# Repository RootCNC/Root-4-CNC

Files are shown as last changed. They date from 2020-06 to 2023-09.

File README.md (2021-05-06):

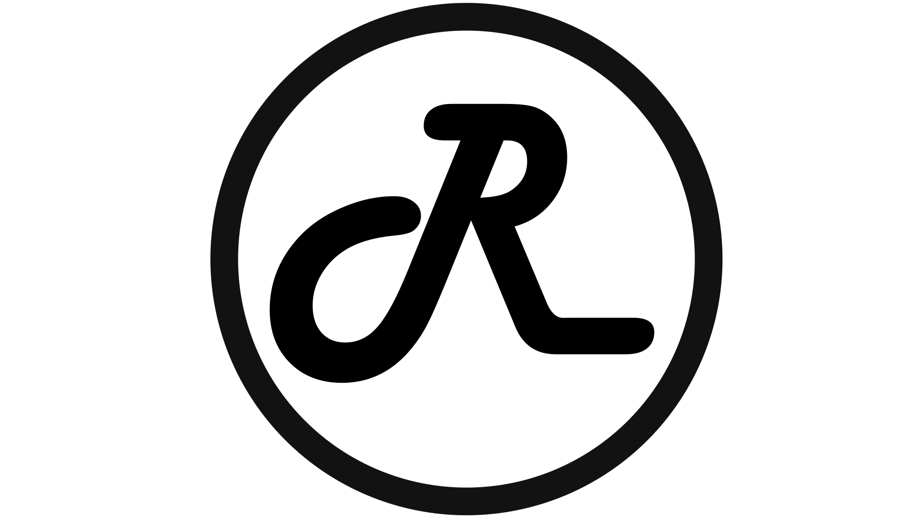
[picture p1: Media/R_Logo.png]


# Root 4 CNC Large Scale 3D Printed CNC Machine
Root 4 is the successor to Root 3 CNC that was my main CNC for a number of years. In fact, there is nothing wrong with my Root 3 CNC (originally named Root 2.1) and it did all my CNC jobs!

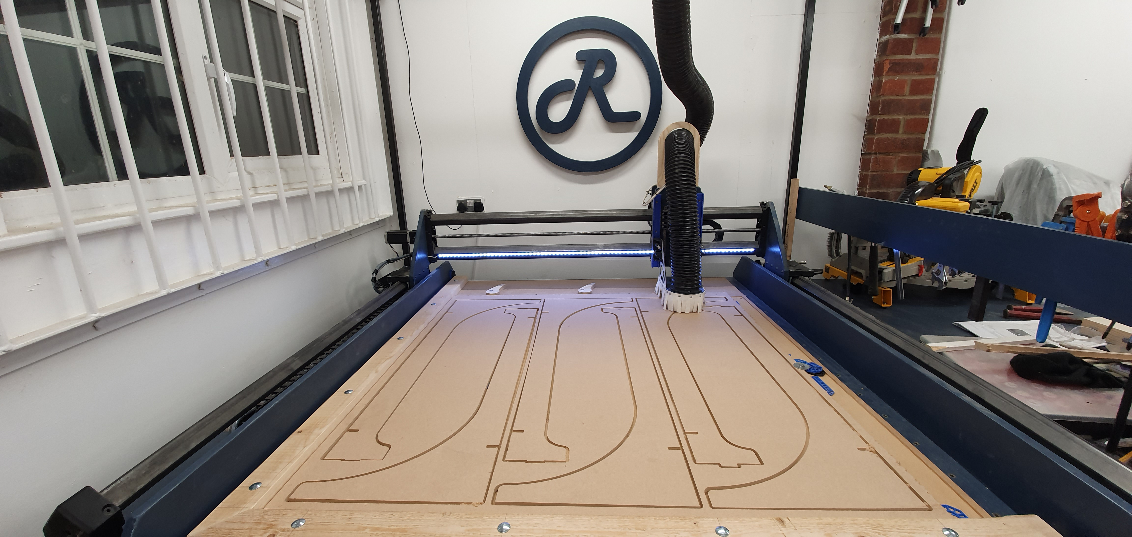
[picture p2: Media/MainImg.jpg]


Root 4 was designed to accommodate larger size 3D printed CNC machine and seeing we’re due to get married soon (Pending lockdown restrictions) – I thought it best to build a bigger one for all the custom wedding ideas we’ve got.

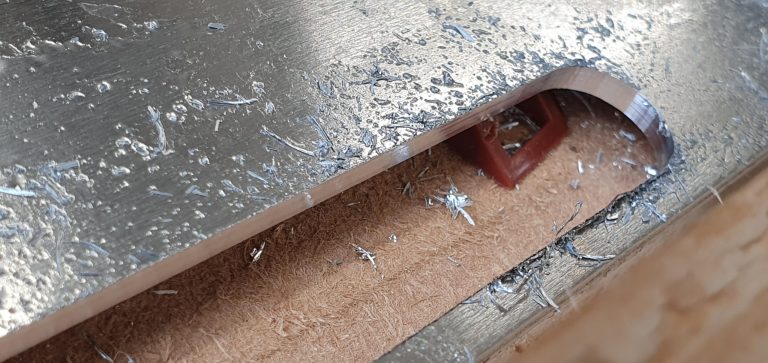
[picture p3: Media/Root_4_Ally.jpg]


The Root 4 follows the core design methodology of simple, cheap, scalable and use common parts for it design. It has also taken inspiration from fellow Root CNC community members who have built their own large-scale 3D printed CNC machines. I do enjoy seeing what you do with these machines, so please consider dropping me an email or post a photo of your build and what you make with this machine.

 ## Key Changes
 A comparison of all the machine can be found on the home page [(LINK)](https://rootcnc.com/)
 1.  Uses 40x40mm Box section
2.  Natively supports balls screws
3.  Has an auto square functionality.
4.  Independent dust shoe.
5.  Stiffer design
6.  Larger working area.

Most of the parts have been tweak from the original Root 3 build but it all can be printed on a standard 200x200mm 3D printer.
## BOM (Bill of Materials)
Bill of Materials can be found [HERE](https://rootcnc.com/root-4-bill-of-materials/)

## Working Area

    What is the working area of the Root 4 CNC Machine?

    What length of 40x40mm Box section do I required?

Please see this file: [Here](https://github.com/RootCNC/Root-4-CNC/blob/master/Working%20Area.xlsx)

For a comparison of **SFU1605 Ball screw length** VS **Box Section Length** VS **working area** (taking into account side panel thickness).

For my build I used 1500mm long ballscrew for both X and Y Axis with a total working area of **1204mm by 1190mm** (XY) with a Z travel of 158mm as standard. (Z-Axis is **not** user configurable)

## Videos
Youtube Videos can be found  [Here](https://www.youtube.com/sailorpete12)

Time Lapse Voice over video series  [Here](https://www.youtube.com/playlist?list=PL5hghy18PulVQLauypyohv9KJJGx_RQMZ)
### Assembly Videos
(http://www.youtube.com/watch?v=JoyMASlxskQ "")
### Detailed Videos
(http://www.youtube.com/watch?v=6tHN1ftT5lI "")
## In action!
(http://www.youtube.com/watch?v=OX2FyZha2Zk "")
(http://www.youtube.com/watch?v=DdyRnfVLRq8 "")
(http://www.youtube.com/watch?v=58G44EHEyc4 "")

## License

This project is licensed under the Creative Commons 4.0 license with 
Attribution-NonCommerial-ShareAlike see `LICENSE.txt` for details

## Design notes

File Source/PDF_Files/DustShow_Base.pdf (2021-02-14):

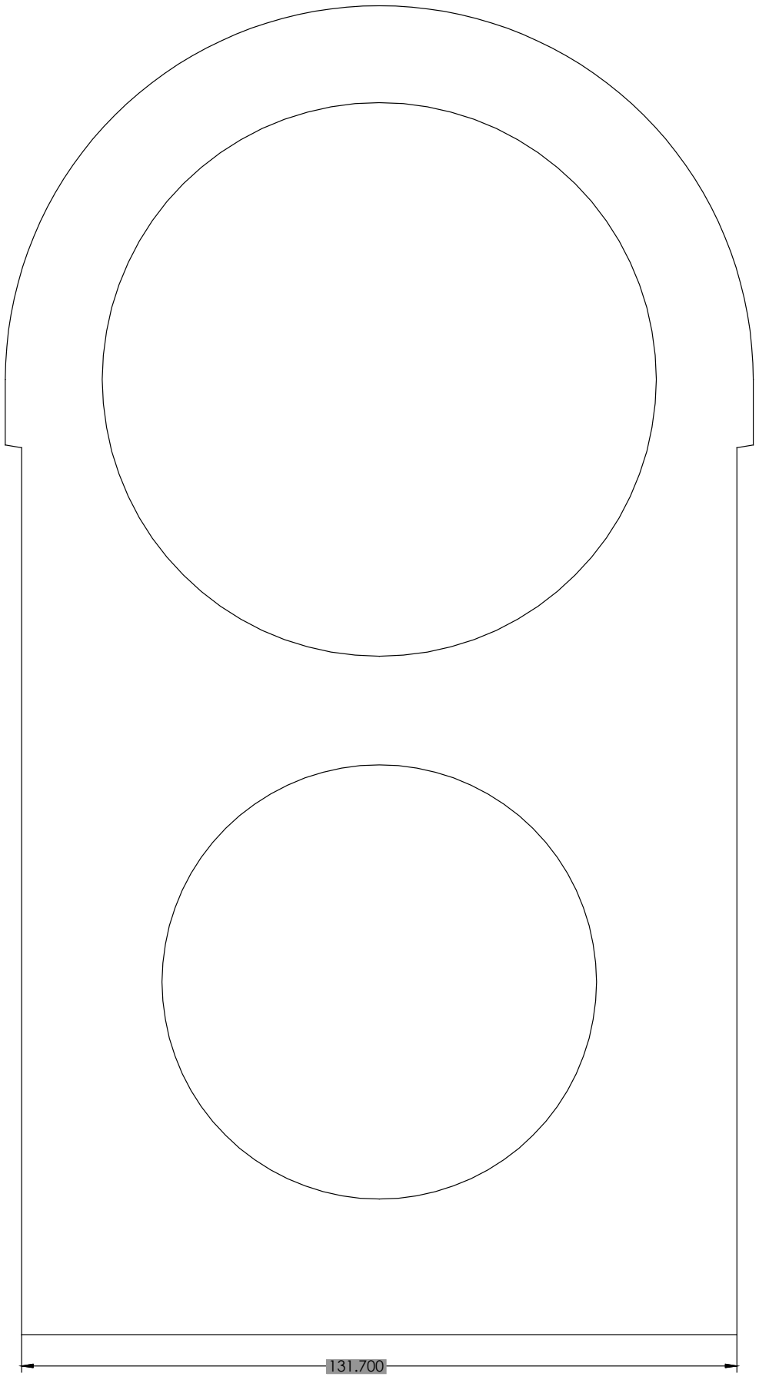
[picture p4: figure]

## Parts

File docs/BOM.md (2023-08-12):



# 3D Printed Parts required

| 3D Printed Parts | Required | QTY |
|---|---|---|
| DustShoe_100mmHose | NO | 1 |
| DustShoe_RailClamp_Left | NO | 1 |
| DustShoe_RailClamp_Right | NO | 1 |
| DustShoe_T_SlotTrack | NO | 2 |
| Spindle_Mount_65mm | YES | 1 |
| X_Axis_DragChainBrace | YES | 1 |
| X_Axis_DragChainBrace (Mirrored) | YES | 1 |
| X_Axis_DragChainMountXCarriage | YES | 1 |
| X_Axis_Mount_FF | YES | 1 |
| X_Axis_Mount_FK | YES | 1 |
| X_Axis_NEMA23_50mmSpacerFK12 | YES | 1 |
| XY_Carriage | YES | 8/4* |
| XY_Carriage_Coach | YES | 4* |
| XY_Axis_BallScrewMount | YES | 3 |
| XY_Axis_BallScrewMount+0.25 | YES | 3** |
| Y_Axis_DragChainCarriageMount | YES | 1*** |
| Y_Axis_Mount_FF12 | YES | 2 |
| Y_Axis_Mount_FK12 | YES | 2 |
| Y_Axis_NEMA23_50mmMotorSpacer | YES | 2 |
| Z_Axis_MotorMount | YES | 1 |

(\*) When Coach bolts are used

(\*\*) Only required if the standard is too loose

(\*\*\*) Can be mirrored for the Drag chain to be mounted on the other side

# Panels
| Item | QTY | Link|
|---|---|-----|
|DustShoe_Side| 2|Root CNC Store|
|DustShoe_Base|1|Root CNC Store|
|Side_Panel_Left_FK|1|[Root CNC Store](https://rootcnc.com/product/root-4-side-panel/)|
|Side_Panel_Right_FF|1|[Root CNC Store](https://rootcnc.com/product/root-4-side-panel/)|
|Z_Axis_WoodPanel_Front|1|Root CNC Store|
|Z_Axis_WoodPanel_Rear|1|Root CNC Store|

# Electronics/ Electro Mechanical
| Item | Required | QTY | Link|
|---|---|---|-----|
| 4 Axis CNC Router Kit 3.0 Nm 425o/in Nema 23 | Yes | 1 | [LINK](https://www.omc-stepperonline.com/4-axis-cnc-router-kit-3-0-nm-425oz-in-nema-23-stepper-motor-driver-power-supply-4-dm542y-23he45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)
|1.5KW Spindle with VFD|Yes|1|[LINK_1](https://s.click.aliexpress.com/e/_dX0JKm3) [LINK_2](https://s.click.aliexpress.com/e/_dT4xs63) [LINK_3](https://s.click.aliexpress.com/e/_dSjt6gr) [LINK_4](https://s.click.aliexpress.com/e/_dSUhh43)
|Micro Switch SPDT micro switch V4 KW11i|Yes|6|[LINK UK](https://amzn.to/31Kf1wC) [LINK](https://s.click.aliexpress.com/e/_ATnQCz)| 
|12V or 24V PSU (For Controller power + any lights) |Yes|1|[12V_LINK_UK](https://amzn.to/2HxYvIS) [12V_lINK](https://s.click.aliexpress.com/e/_AACYyd)| 
|Electrical Cabinet (size greater than 400x400x200mm) |No|1|| 
|Aviation plug (GX12) |No|x|[LINK_UK](https://amzn.to/31LBPfl)[LINK](https://s.click.aliexpress.com/e/_AtqbWz)|

# Motion
| Item | Required | QTY | Link|
|---|---|---|-----|
|608 Bearings | Yes | 38 |[LINK_UK](https://amzn.to/3dWB9c6) [LINK](https://s.click.aliexpress.com/e/_ATuujF)|
|SFU1605 L300 (Z-Axis) | Yes | 1 |[LINK_UK](https://amzn.to/3osWWNp) [LINK](https://s.click.aliexpress.com/e/_AOHs9J)|
|SFU1605 L### (X-Axis) | Yes | 1 |[LINK_UK](https://amzn.to/35AbBOe) [LINK](https://s.click.aliexpress.com/e/_9zA1ff)|
|SFU1605 L### (Y-Axis) | Yes | 2 |[LINK_UK](https://amzn.to/35AbBOe) [LINK](https://s.click.aliexpress.com/e/_9zA1ff)|
|FK12 Bearing | Yes | 3 |[LINK_UK](https://amzn.to/35zBhKN) [LINK](https://s.click.aliexpress.com/e/_9v05o1)|
|FF12 Bearing | Yes | 3 |[LINK_UK](https://amzn.to/35zBhKN) [LINK](https://s.click.aliexpress.com/e/_9v05o1)|
|BK12 | Yes | 1 |[LINK](https://s.click.aliexpress.com/e/_9v05o1)|
|BF12 | Yes | 1 |[LINK](https://s.click.aliexpress.com/e/_9v05o1)|
|MGN12 250mm + (MGN12C x2) | Yes | 2 |[LINK](https://s.click.aliexpress.com/e/_ALbQTF)|
|R38 18mm x 37mm Black Drag Chain 1M | Yes | CNC Size dependant |[LINK_UK](https://amzn.to/37J6PAH)  [LINK](https://s.click.aliexpress.com/e/_9hJS33)|
|T-track [300mm, Blue] | Yes | 2 |[LINK_UK](https://amzn.to/3mkDBvK) [LINK](https://s.click.aliexpress.com/e/_9x8Pnf)|
|CNC shaft couplers Spider Jaw (10mm to 10mm)| Yes | 3 |[LINK_UK](https://amzn.to/3jxH1tx) [LINK](https://s.click.aliexpress.com/e/_AP8YPT)|
|HTD 3M Round Tooth Timing Belt Pulley 10MM Bore 36T| Yes | 1 |[LINK](https://s.click.aliexpress.com/e/_9hO2OZ)|
|HTD 3M Round Tooth Timing Belt Pulley 10MM Bore 36T*| Yes | 1 |[LINK](https://s.click.aliexpress.com/e/_9hO2OZ) |
|HTD 3M Round Tooth Timing Belt 9mm Wide 474-3m-09| Yes | 1 |[LINK_UK](https://amzn.to/2Tu7xcu) [LINK](https://s.click.aliexpress.com/e/_9HpJZj)

(\*) Dependant on stepper motor selection - This configuration will work for the above stepper motor from OMC Stepper Motor Online
# Hardware
Below is guide on the QTY required/ the pack sizes I brought to assemble the Root 4 CNC
| Item | Required | QTY | Link|
|---|---|---|-----|
|40mm box section (50mm shorter than X lead screw) *|Yes|2||
|40mm box section (70mm shorter than Y lead screw ONLY WITH 18MM SIDE PANELS!) *|Yes|2||
|M3 Insert Nut (Z-Axis Linear Guilds) | Yes | 20  | | 
|M3 X 14MM Allen Hex Head A4 (Z-Axis Carriage to linear guilds) | Yes | 16  | | 
|M3 X 16MM Allen Hex Head A4 (Z-Axis linear Guilds) | Yes | 20  | | 
|M4 Knurled Thumb Nut (Used for Independent height dust shoe) | No | 4  | | 
|M4 Nut | Yes | 100  | | 
|M4 Penny Washer | Yes | 100  | | 
|M4 X 10mm Socket Cap Head  | Yes | 100  | | 
|M4 X 20mm Socket Cap Head  | Yes | 100  | | 
|M4 X 25mm Socket Cap Head  | Yes | 100  | | 
|M4 X 30mm Socket Cap Head  | Yes | 100  | | 
|M4 X 40MM COUNTERSUNK | Yes | 100  | | 
|M4 X 40mm Socket Cap Head  | Yes | 100  | | 
|M5 Knurled Thumb Nut (Used for Independent height dust shoe) | No | 2  | | 
|M5 Nuts  | Yes | 100  | | 
|M5 Washer | Yes | 100  | | 
|M5 x 16mm Socket Cap Head (To secure the Ball screw to Ball screw block, Z-Carriage) | Yes | 28  | | 
|M5 x 20mm Socket Cap Head | Yes | 50  | | 
|M5 x 55mm Socket Cap Head | Yes | 8 | |
|M5 x 75mm (Used for independent height dust shoe) | Yes | 4  | | 
|M5 X 90MM A2 STAINLESS STEEL CAP HEX HEAD | Yes | 20  | | 
|M6 Bed Insert nut | No | 200  | | 
|M6 Insert Nut (10MM Long Furniture Insert) | Yes | 6  | | 
|M6 x 10 mm Socket Cap Head | Yes | 20  | | 
|M6 x 40mm Socket Cap Head (Z-Axis Ball screw bearing block) | Yes | 6  | | 
|M8 loc nut | Yes | 100  | | 
|M8 Nut | Yes | 200  | | 
|M8 Washer | Yes | 200  | | 
|M8 x 100mm (Coach or STD) Bolt | Yes | 16  | | 
|M8 X 25MM  | Yes | 38  | | 

(\*) Please see this file [Here](https://github.com/RootCNC/Root-4-CNC/blob/master/Working%20Area.xlsx). For a comparison of **SFU1605 Ball screw length** VS **Box Section Length** VS **working area** (taking into account side panel thickness).

# MISC Items
| Item | Required | QTY | Link|
|---|---|---|-----|
|Mist Coolant Lubrication Spray System Unit (Used for Airline to Spindle - Aluminium machining)| No |1 | |
|Pneumatic Air Solenoid Valve 2Way (Used for Airline to Spindle - Aluminium machining)| No |1 | |
|T-track [300mm, Blue]| No |2 | |
|Yellow Semi Rigid Nylon Tubing (Used for Airline to Spindle - Aluminium machining)| No |1 | |
|Male Swivel Elbow Pneumatic Push-In Fitting Connector for Air. Size 8mm x 1/4"| No |x | |

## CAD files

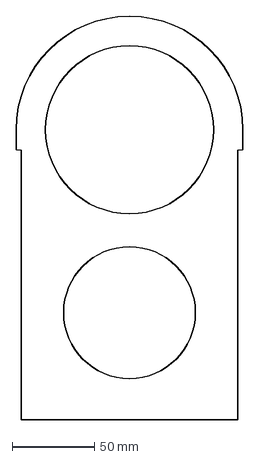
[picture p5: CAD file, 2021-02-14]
Source/DXF_Files/DustShoe_Base.DXF
137.7 x 244.9 mm

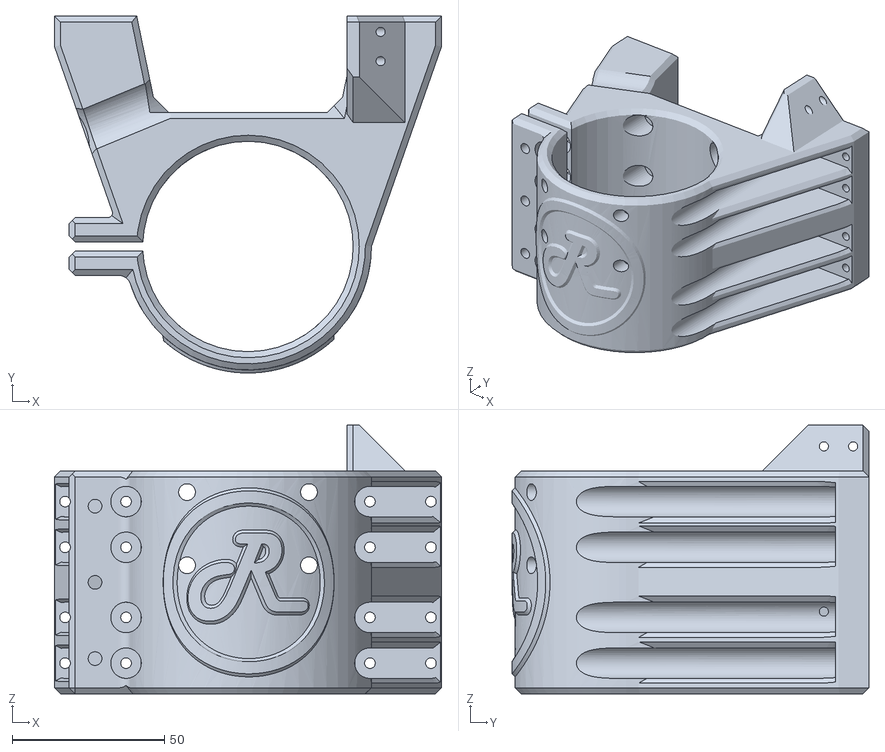
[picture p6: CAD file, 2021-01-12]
Source/STL_Files/Spindle_Mount_69mm.STL
127.0 x 117.1 x 88.2

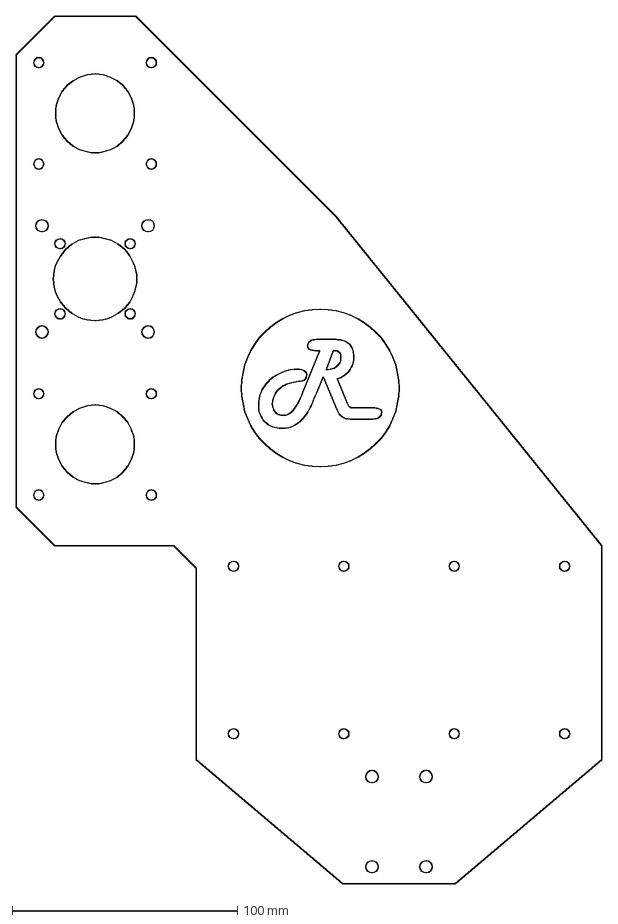
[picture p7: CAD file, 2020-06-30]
Source/DXF_Files/Side_Panel_Left_FK.DXF
260.0 x 385.0 mm

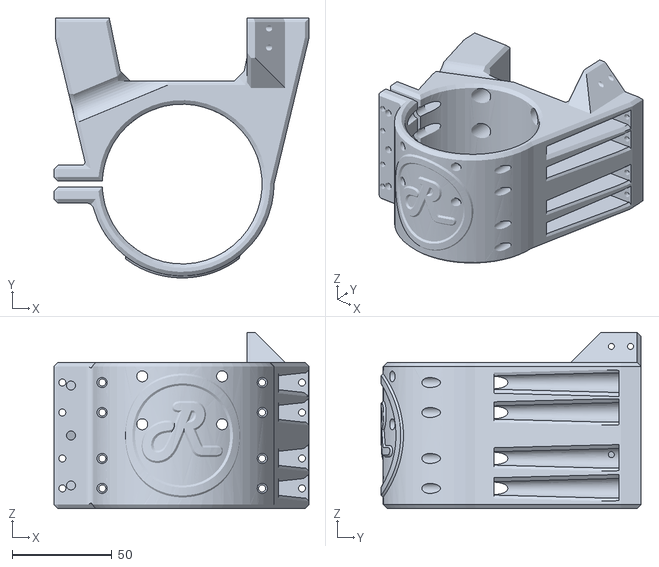
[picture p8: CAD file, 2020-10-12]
Source/STL_Files/Spindle_Mount_80mm.STL
127.7 x 130.1 x 88.2

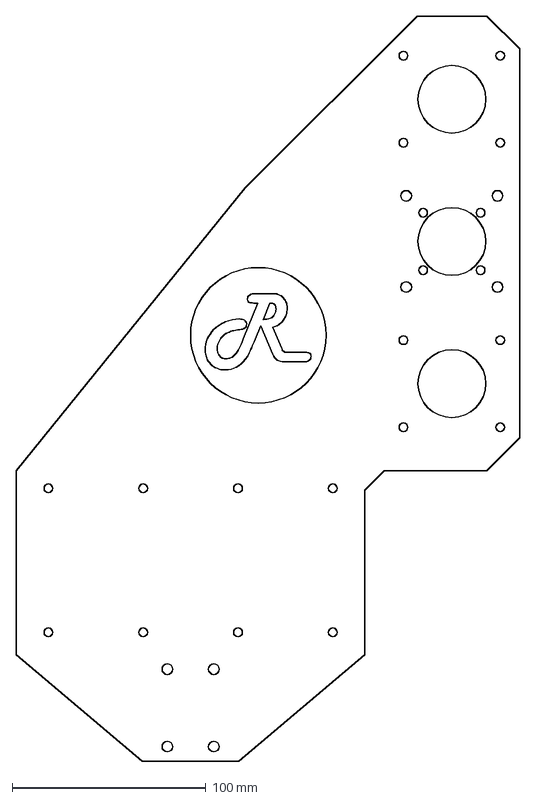
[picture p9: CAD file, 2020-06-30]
Source/DXF_Files/Side_Panel_Right_FF.DXF
260.0 x 385.0 mm

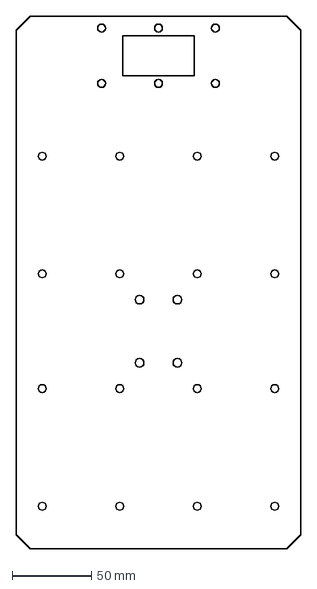
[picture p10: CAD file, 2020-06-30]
Source/DXF_Files/Z_Axis_WoodPanel_Rear.DXF
180.0 x 337.0 mm

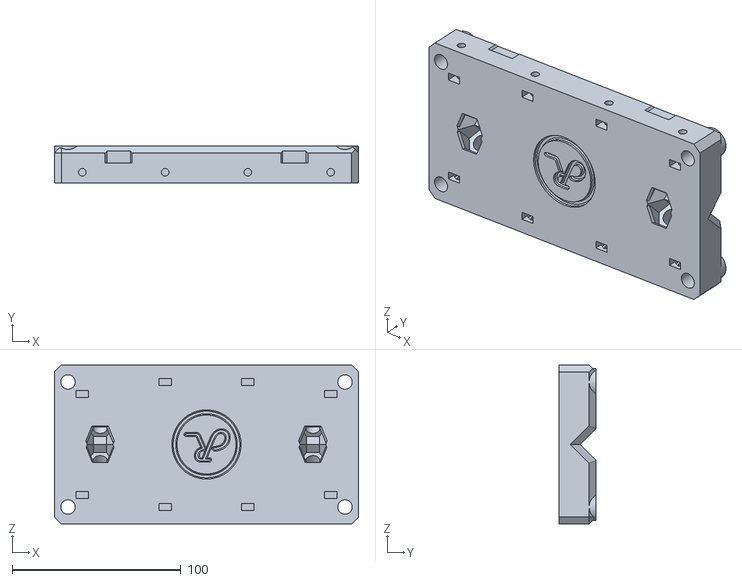
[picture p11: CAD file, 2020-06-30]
Source/STL_Files/XY_Carriage.STL
180.0 x 22.2 x 94.0

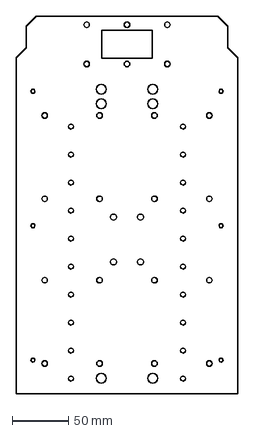
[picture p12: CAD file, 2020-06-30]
Source/DXF_Files/Z_Axis_WoodPanel_Front.DXF
198.0 x 337.0 mm

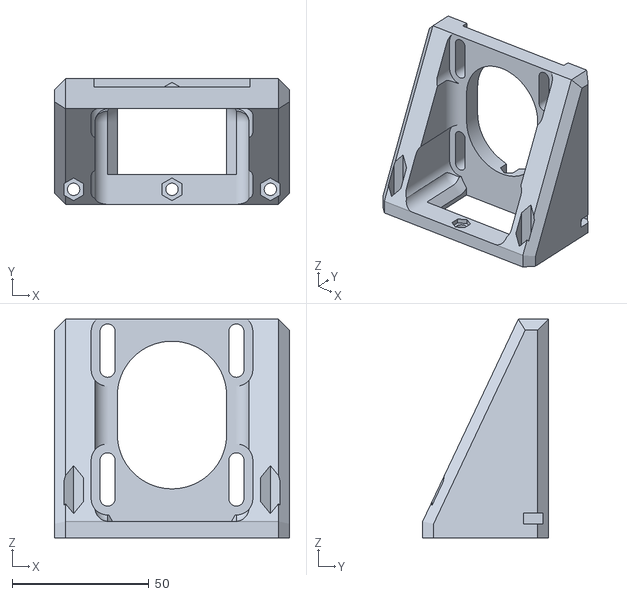
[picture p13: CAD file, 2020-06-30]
Source/STL_Files/Z_Axis_MotorMount.STL
86.0 x 46.0 x 80.0

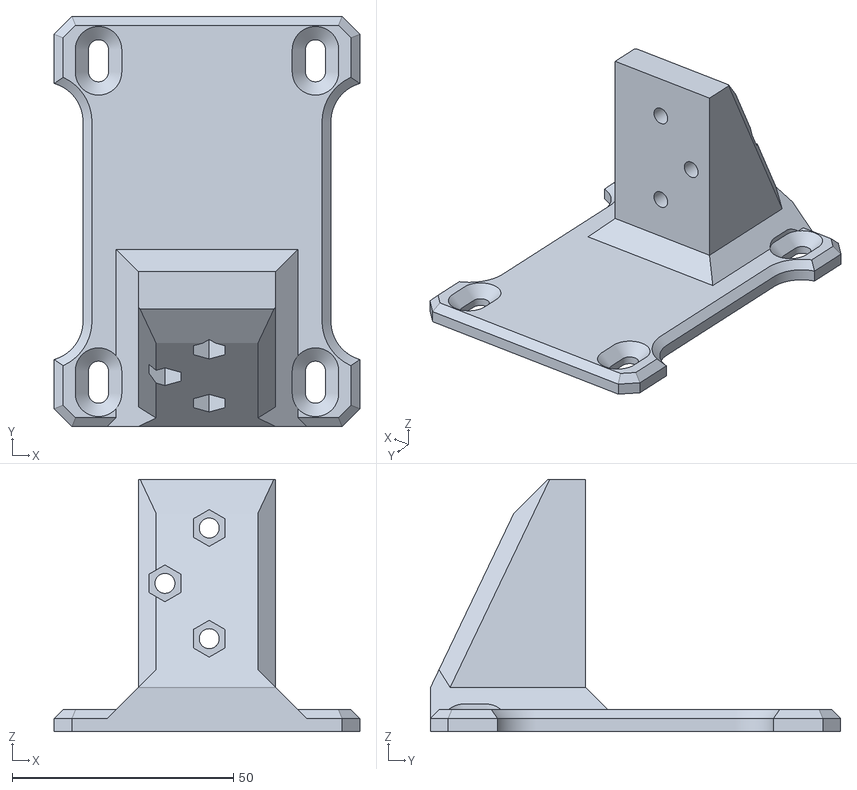
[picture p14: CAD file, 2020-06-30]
Source/STL_Files/X_Axis_DragChainMountXCarriage.STL
69.0 x 92.6 x 57.0

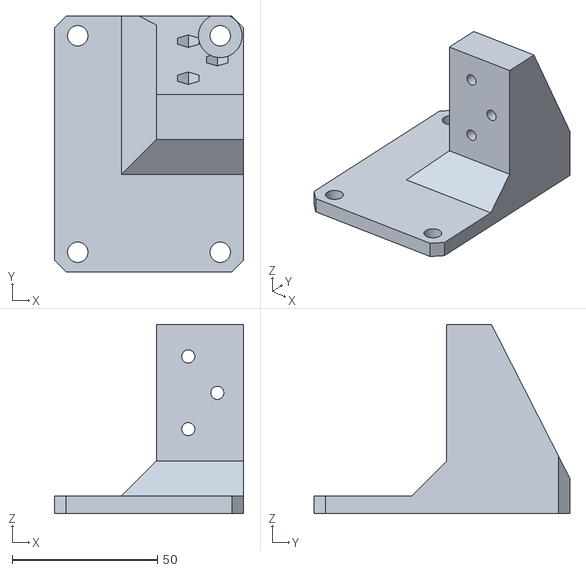
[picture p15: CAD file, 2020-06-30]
Source/STL_Files/Y_Axis_DragChainCarriageMount.STL
65.0 x 88.0 x 65.0

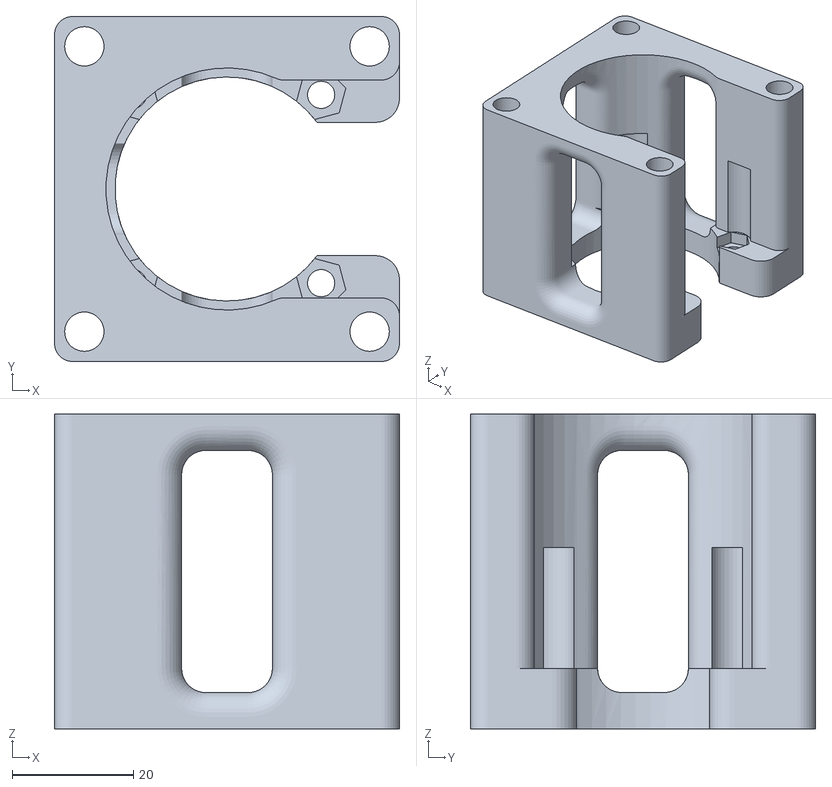
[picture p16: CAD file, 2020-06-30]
Source/STL_Files/X_Axis_NEMA23_50mmSpacerFK12.STL
57.0 x 57.0 x 52.0

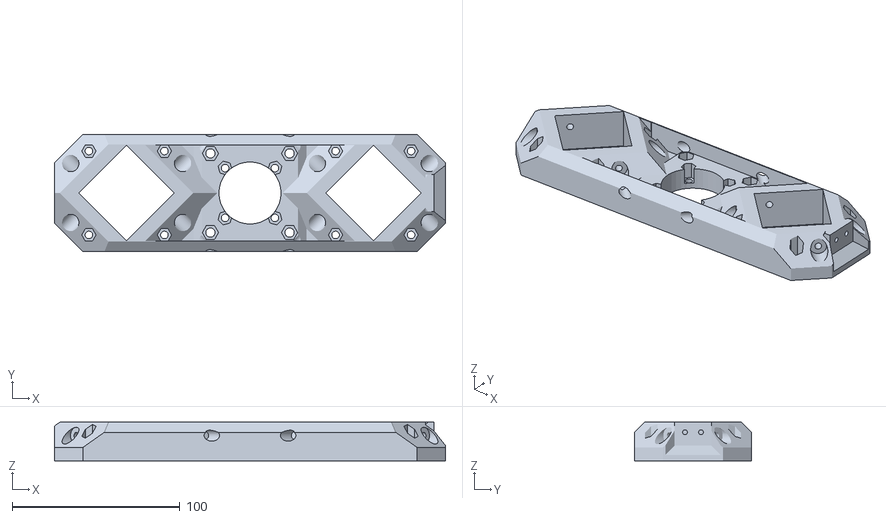
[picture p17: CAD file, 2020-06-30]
Source/STL_Files/X_Axis_Mount_FF.STL
233.0 x 70.0 x 23.0

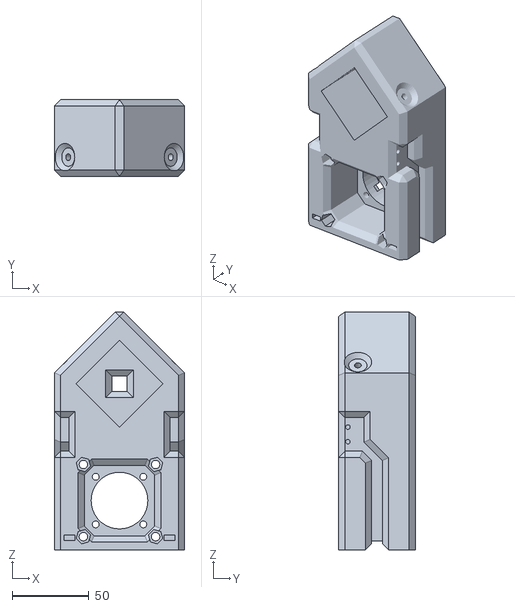
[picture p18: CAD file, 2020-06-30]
Source/STL_Files/Y_Axis_Mount_FF12.STL
85.0 x 50.0 x 155.4

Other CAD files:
Source/STL_Files/DustShoe_T_SlotTrack.STL
Source/STL_Files/Y_Axis_NEMA23_50mmMotorSpacer.STL
Source/STL_Files/X_Axis_Mount_FK.STL
Source/STL_Files/X_Axis_DragChainBrace.STL
Source/DXF_Files/DustShoe_Side.DXF
Source/STL_Files/DustShoe_Side.STL
Source/STL_Files/XY_Axis_BallScrewMount+0.25.STL
Source/STL_Files/XY_Axis_BallScrewMount.STL
Source/STL_Files/XY_Carriage_Coach.STL
Source/STL_Files/Y_Axis_Mount_FK12.STL

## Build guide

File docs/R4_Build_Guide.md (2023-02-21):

---
title: Root 4 Assembly Guide
description: Root 4 Assembly Guide 
published: true
date: 2022-06-28T21:37:30.411Z
tags: root 4, r4, guide
editor: markdown
dateCreated: 2022-05-24T19:30:47.756Z
---

# Root 4 CNC Build Guide

## Before you get building/printing

## Key info
1.  Build area and machine size is all dependent on the size of ball screws and box section. Please see this file: [Here](https://github.com/RootCNC/Root-4-CNC/blob/master/Working%20Area.xlsx)
2.  North American builders should see the gotchas below
3.  Ballpark price is dependent on your build size and upgrade/quality-of-life choices you make, but expect somewhere in the realm of £900-1200 GBP, $1200-1500 USD, $1500-2000 AUD

## Gotchas before starting
1. Make sure you have access to metric box section in your country before you start printing parts.
2. If you need Imperial, then there is a [branch of files for 1.5 inch box section to print instead](https://github.com/RootCNC/Root-4-CNC/tree/38mm-Dev/Source/STL_Files/38.1x38.1mm%20Box%20Section%20%281.5x1.5%20inch%29)

## Printing parts

### Printing considerations
1. If you have access to a 0.6mm nozzle, this will significantly decrease the time needed to print, while also strengthening the parts due to the line widths. **Worth buying one just for this project alone.**
2. Similarly, larger layer heights afforded by the 0.6mm nozzle will give you more strength and speed up the print
3. Rigidity of material matters as much as strength for a number of parts. Consider using a modified PLA blend (commonly known as PLA+, pro PLA etc.) for parts where rigidity is paramount (see table below) and PETG for parts where sheer strength is more important.
4. More walls is better than more infill if you want strong parts
5. Use supports really carefully - some models have quite complex segments for nestling hex nuts, and you don't want to be pulling supports out of those spots. Use support blockers to ensure those channels are kept clear.
6. Tune your printer to give you accurate hole diameters. Check every hole after printing before moving on to print a duplicate part.

### Recommended print settings
1. 2-3 walls/perimeters of 0.6mm width
2. 0.3+ layer heights - this can be achieved with a 0.4mm nozzle, but better with a 0.6mm nozzle. Adaptive layers not recommended.
3. 3-4 bottom/top layers - whether you choose 3 or 4 will depend on whether there are mounting holes pushing against the top/bottom.
4. 30-40% infill. The more a piece is likely to be compressed, the more infill. If approaching 40% infill, consider if you'd be better off adding an additional wall instead.
5. None of these parts need to be pretty, so feel free to print as fast as you can, just ensure that your holes are accurate. Use hole horizontal expansion to your advantage to perfect your hole sizes.

## Planning your build
- Use the [working area file](https://github.com/RootCNC/Root-4-CNC/blob/master/Working%20Area.xlsx) to determine what size ball screws and box section you need to order.
- What do you intend to cut on your CNC? Consider whether a square build is most suitable, or whether a wider X axis with a shallower Y axis will mean your CNC takes up a smaller footprint, but can allow larger stock to be fed through from front to back for the occasional larger project.
- Going wider in the X axis is cheaper than going longer in the Y axis, as you only have a single ball screw on the X axis, but the amount of square box section is the same.
- Do you want the lightness and stiffness of aluminium square hollow section (will tend to cost more) or the beefy weight of steel (tends to be cheaper if not shipped). Steel's density will absorb more vibrations from the machine than aluminium will, and it's weight will go a small way to minimising deflection.

## Building your platform
- Decide what base/platform you're going to build your CNC upon. The Root 4 is different to the previous Root machines in that the machine isn't necessarily designed to be portable and doesn't rest on feet. This means you can really make the most of having a rigid platform.
- Keeping the platform square and flat over the life of the machine is essential. There are a few ways to do this:
  - You can follow the method in the videos of welding a metal frame to mount plywood to. This is the simplest and likely most cost effective method. The metal frame will stop the plywood from warping over time and also give you a frame for mounting controls/enclosure on.
  - If you intend to make a timber frame, then you will be best served building a 'torsion box' table to keep the surface as flat as possible. This can be done with an MDF core and two sheets of plywood - just make sure you have solid corners to be able to countersink mount holes for your Y axis mounts.
- Make sure your platform is deep enough to accommodate your stepper motors on their standoffs without hanging over the back of your CNC.
- Make sure your platform is wide enough to accommodate mounting your cable chain outside the path/width of the Y carriage.
- Do you want to use alcohol/alcohol-based cutting fluid for milling metals? Make sure any finish you put on your wood is not going to break down with alcohol or other solvents.

## High level overview - Order of construction
1. Carriages - build them up according to the video, slide them onto the tubes, ensure they have no play.
2. Mount Y axis ball screw mount and aluminium ball screw nut housing onto the Y axis side panels (not essential to do now, but does make things easier)
3. Mount Y axis side panels onto Y carriages (far easier to do now than trying to get in under already mounted square tubes)
4. Mark out and drill your Y axis mount holes. Screw down the rear mount.
5. Slide your hollow box section into the Y axis mount (ensuring the carriages are already on) and screw in the front Y axis mount
6. Prepare the Z axis front panel with rivnuts and threaded inserts, screw on your linear rails, leave everything else off
7. Mount X axis ball screw mount and aluminium ball screw nut housing onto the rear face of the Z axis front panel
8. Slide X axis mounts onto hollow box section (ensuring the carriages are already on) and lay it down on your table
9. Mount the Z axis front panel onto the X carriages
10. Wind the X axis ball screw nut into the centre of the screw. Position the X axis ball screw in place between the box section, ensuring the ball screw nut is on the correct side to nest inside the aluminium housing, but also ensuring the end machined for the fixed ball screw mount (FF) is on the left. Screw the ball screw nut into the housing
11. Flip the X axis setup over and mount the Z axis rear panel
12. Resting your X axis bottom carriage on a box or something of suitable height for support, screw the X axis mounts in place on your side panels
13. Attach your X axis ball screw mounts
14. TBC

## License

This project is licensed under the Creative Commons 4.0 license with 
Attribution-NonCommerial-ShareAlike see `LICENSE.txt` for details

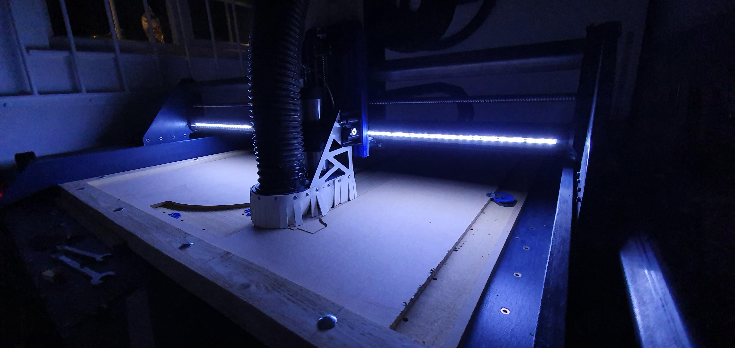
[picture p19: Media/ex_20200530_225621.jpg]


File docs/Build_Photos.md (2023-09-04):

---
title: Root 4 Build Photos
description: Build Photos for the Root 4
published: true
date: 2022-06-28T22:24:57.245Z
tags: root 4, how to print
editor: markdown
dateCreated: 2022-06-28T22:17:17.168Z
---

# Build Photos
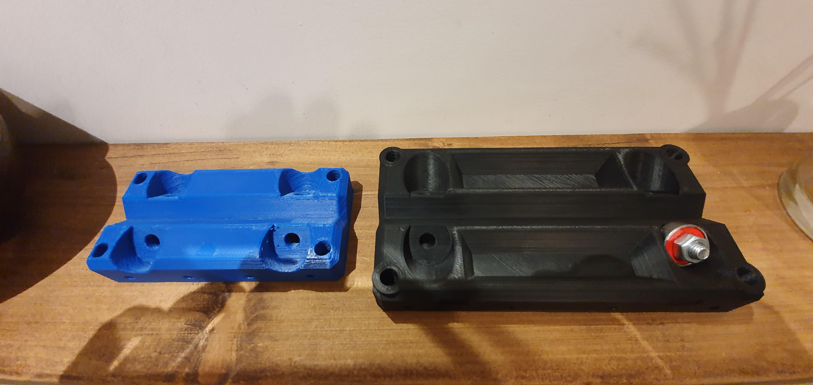
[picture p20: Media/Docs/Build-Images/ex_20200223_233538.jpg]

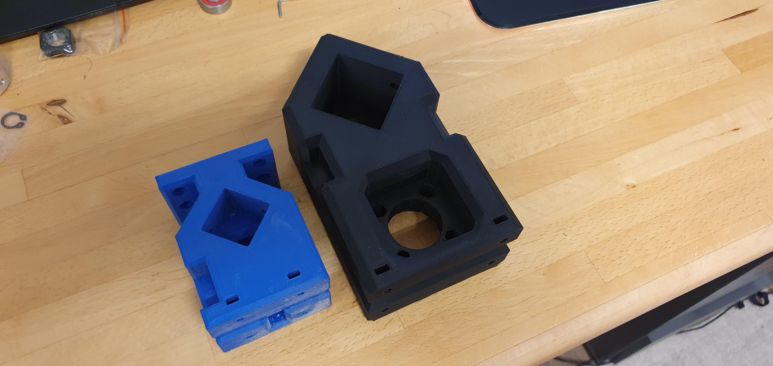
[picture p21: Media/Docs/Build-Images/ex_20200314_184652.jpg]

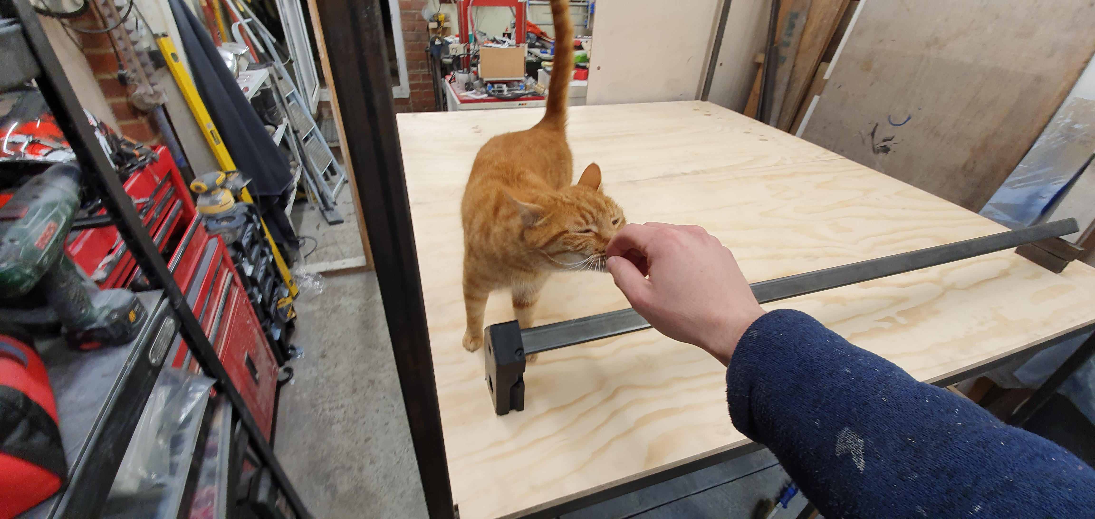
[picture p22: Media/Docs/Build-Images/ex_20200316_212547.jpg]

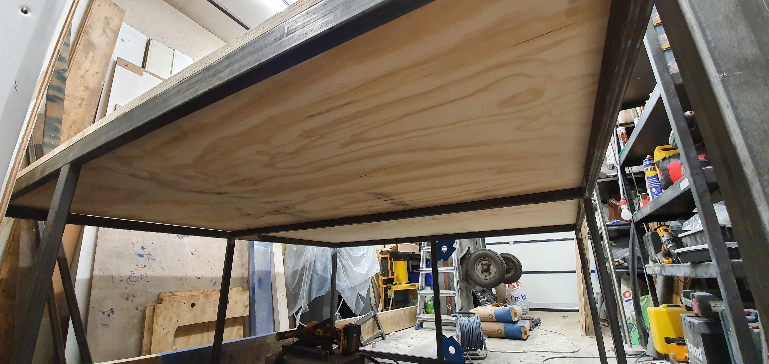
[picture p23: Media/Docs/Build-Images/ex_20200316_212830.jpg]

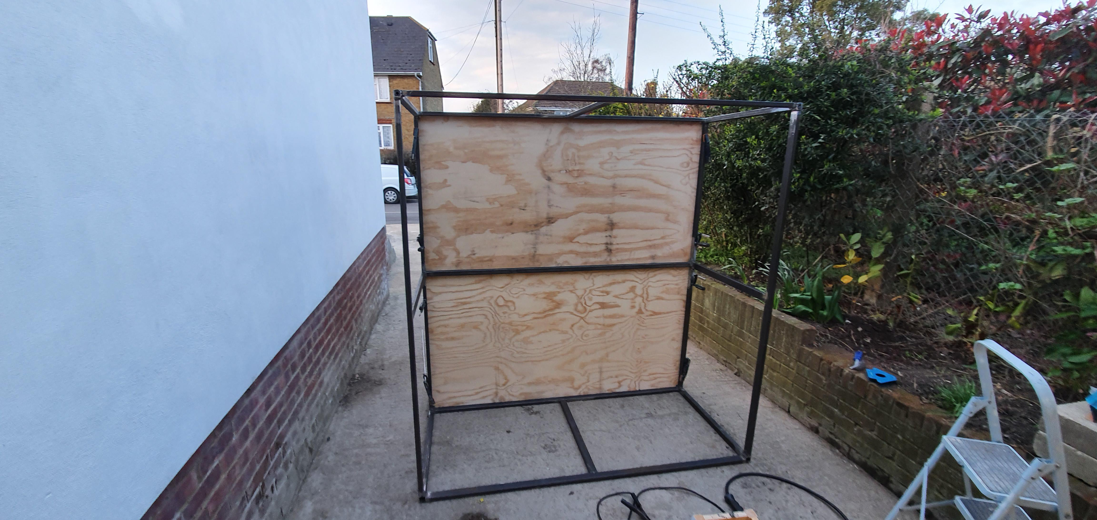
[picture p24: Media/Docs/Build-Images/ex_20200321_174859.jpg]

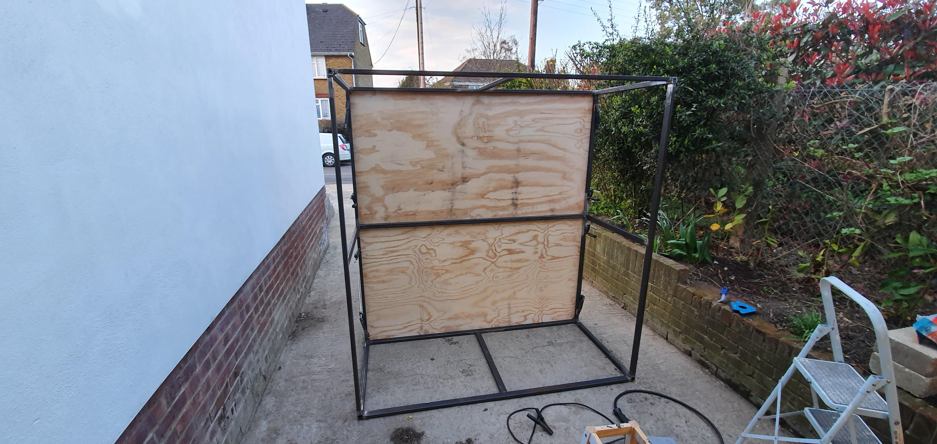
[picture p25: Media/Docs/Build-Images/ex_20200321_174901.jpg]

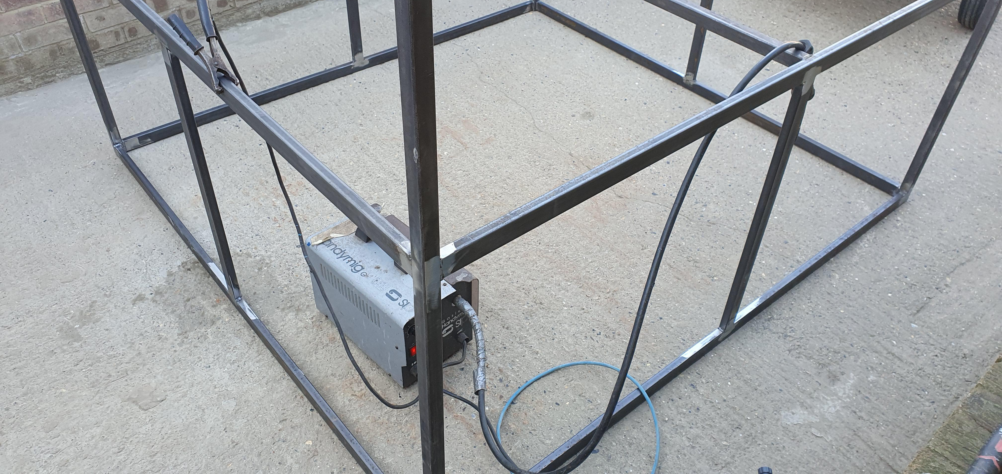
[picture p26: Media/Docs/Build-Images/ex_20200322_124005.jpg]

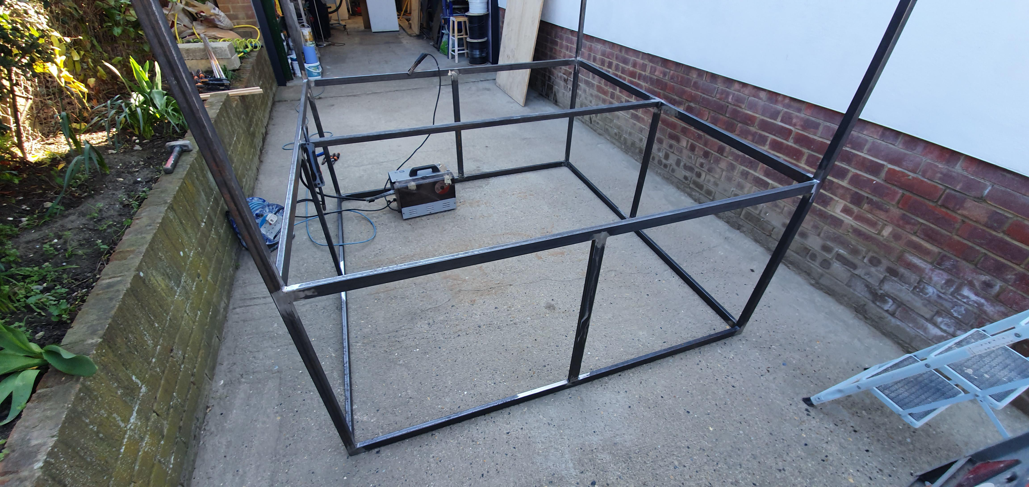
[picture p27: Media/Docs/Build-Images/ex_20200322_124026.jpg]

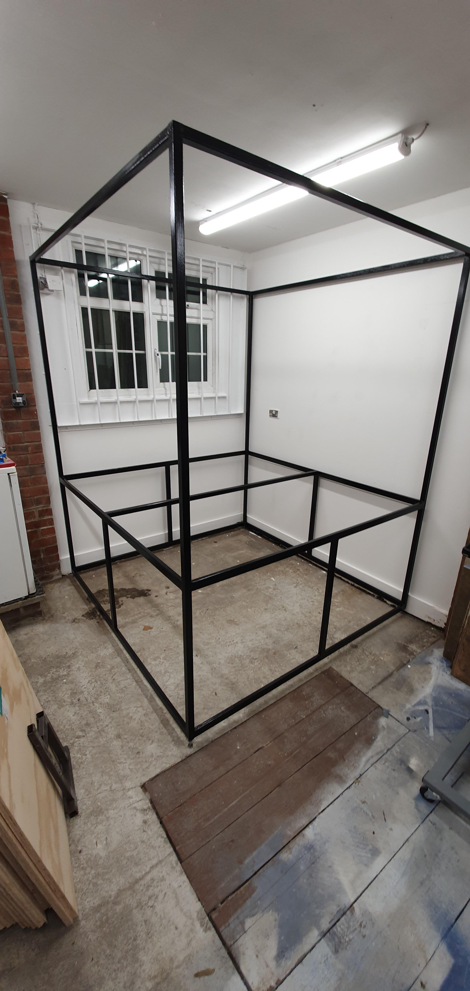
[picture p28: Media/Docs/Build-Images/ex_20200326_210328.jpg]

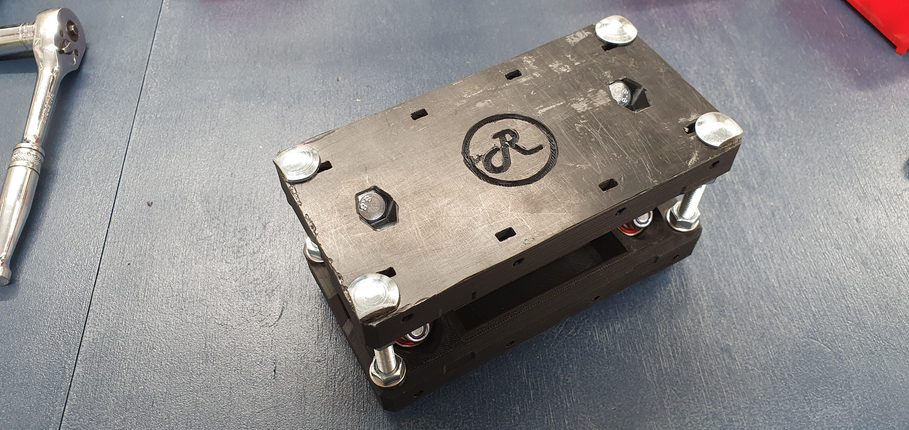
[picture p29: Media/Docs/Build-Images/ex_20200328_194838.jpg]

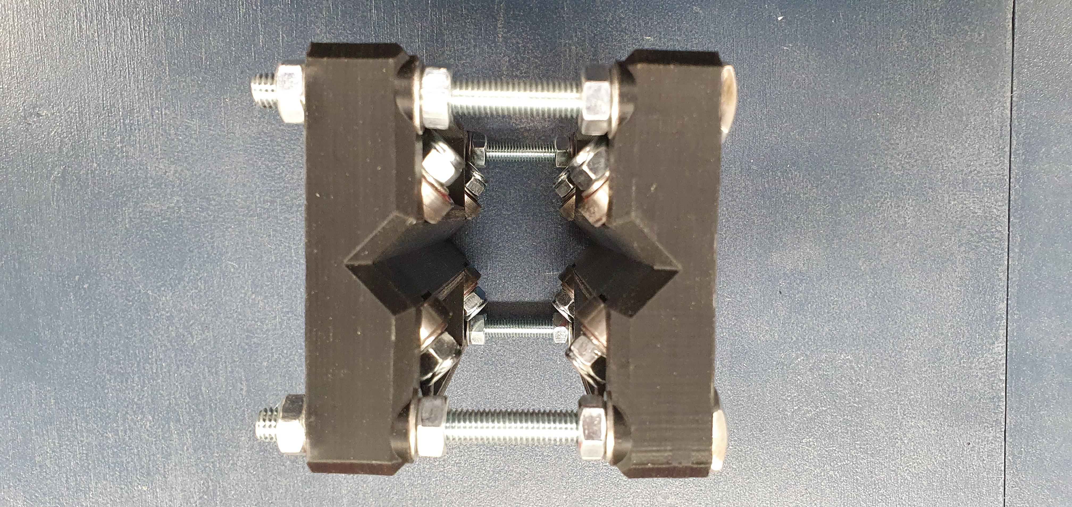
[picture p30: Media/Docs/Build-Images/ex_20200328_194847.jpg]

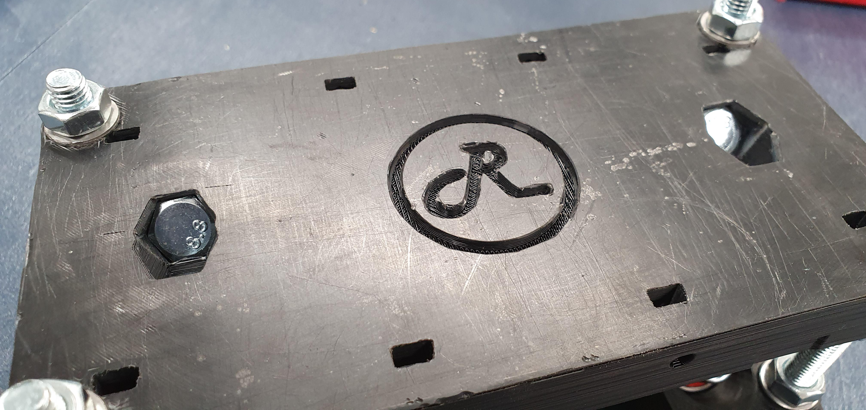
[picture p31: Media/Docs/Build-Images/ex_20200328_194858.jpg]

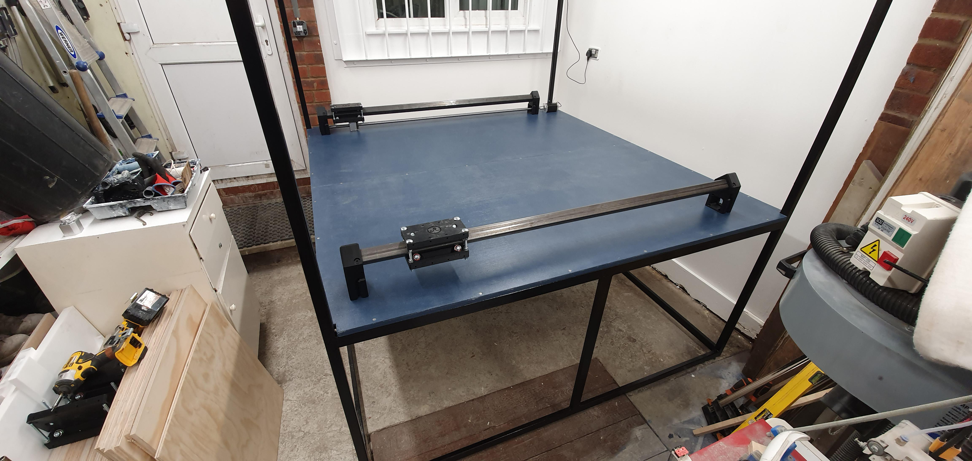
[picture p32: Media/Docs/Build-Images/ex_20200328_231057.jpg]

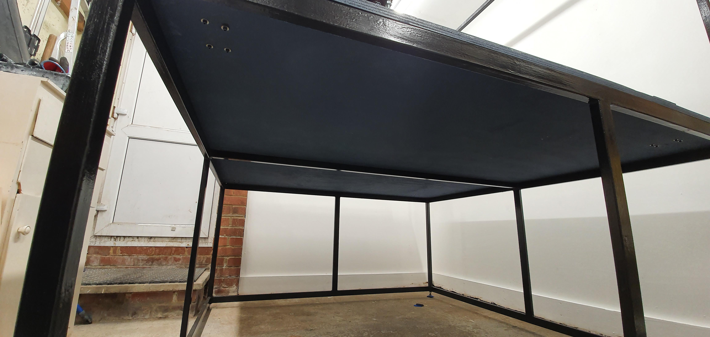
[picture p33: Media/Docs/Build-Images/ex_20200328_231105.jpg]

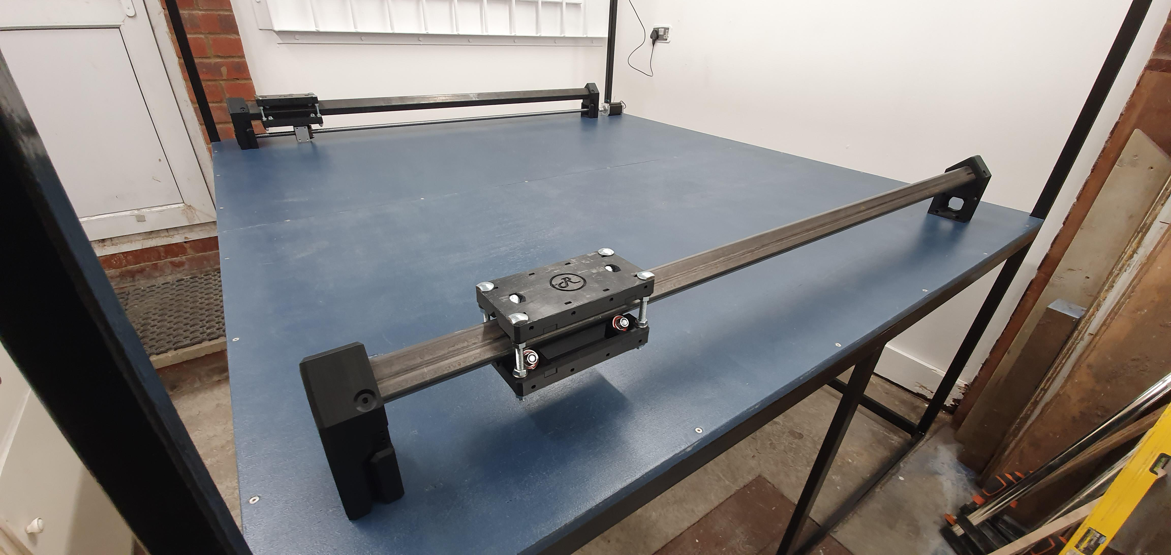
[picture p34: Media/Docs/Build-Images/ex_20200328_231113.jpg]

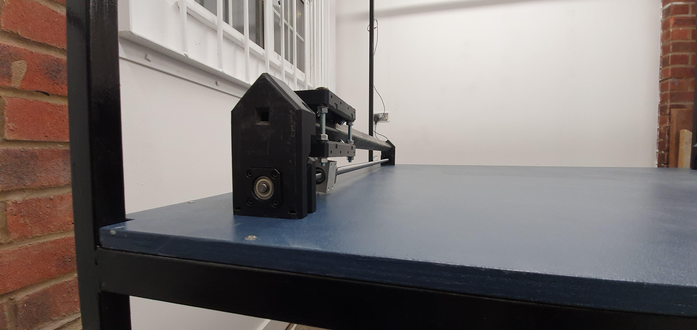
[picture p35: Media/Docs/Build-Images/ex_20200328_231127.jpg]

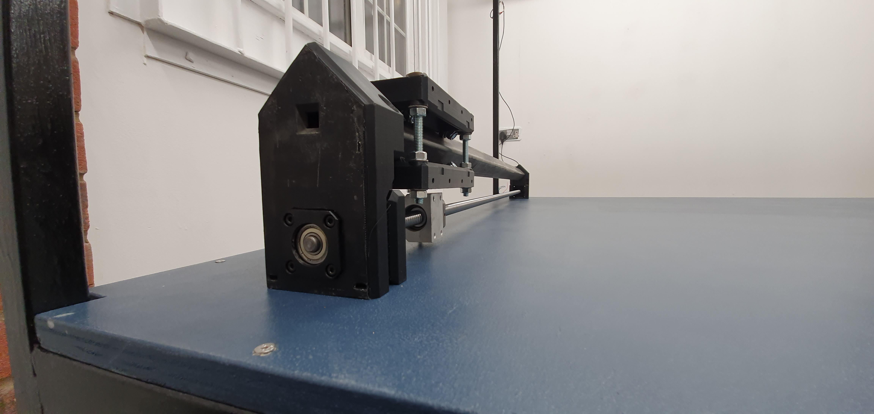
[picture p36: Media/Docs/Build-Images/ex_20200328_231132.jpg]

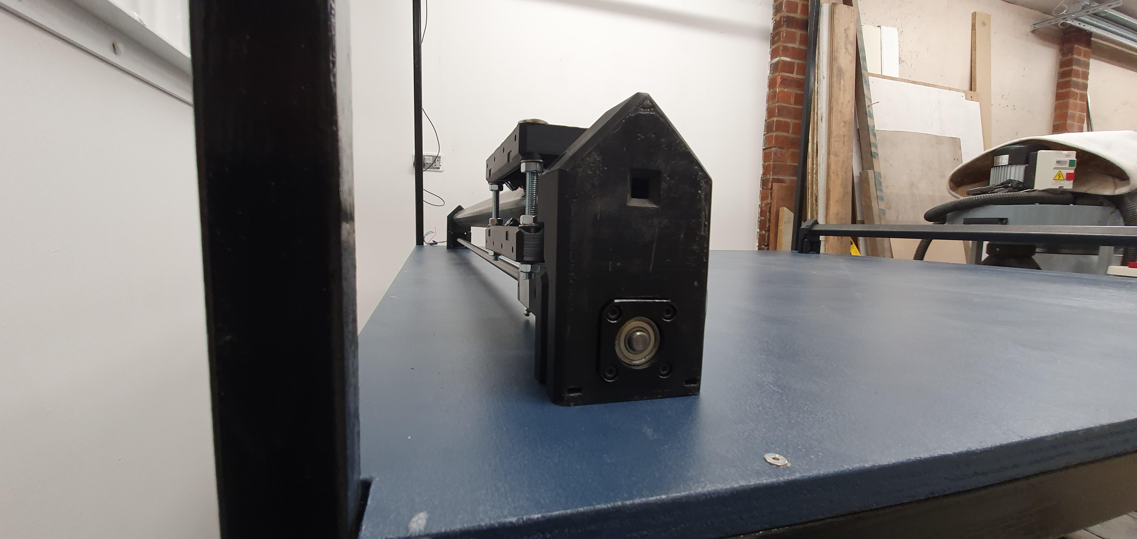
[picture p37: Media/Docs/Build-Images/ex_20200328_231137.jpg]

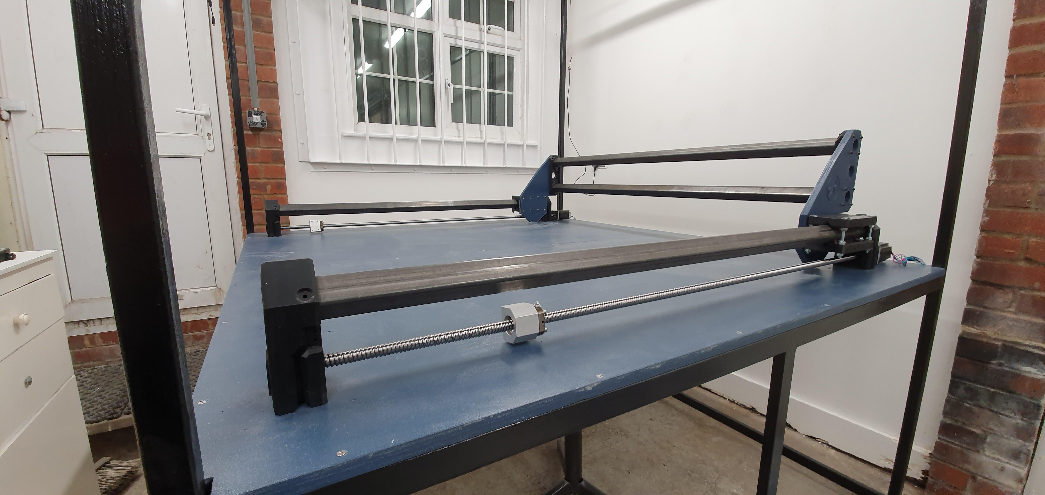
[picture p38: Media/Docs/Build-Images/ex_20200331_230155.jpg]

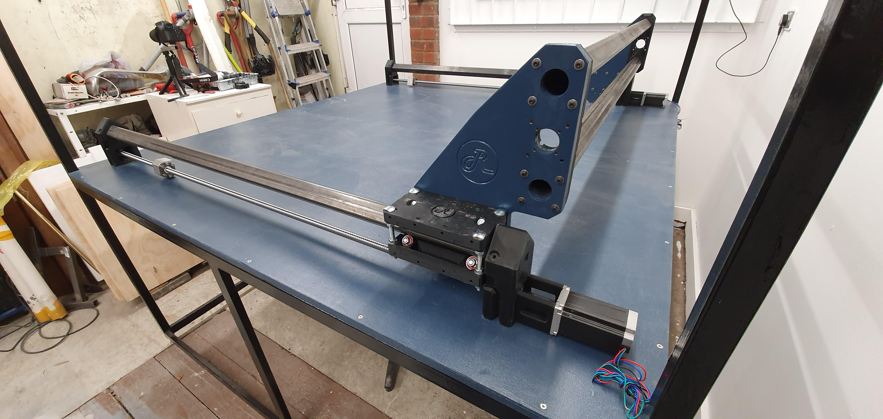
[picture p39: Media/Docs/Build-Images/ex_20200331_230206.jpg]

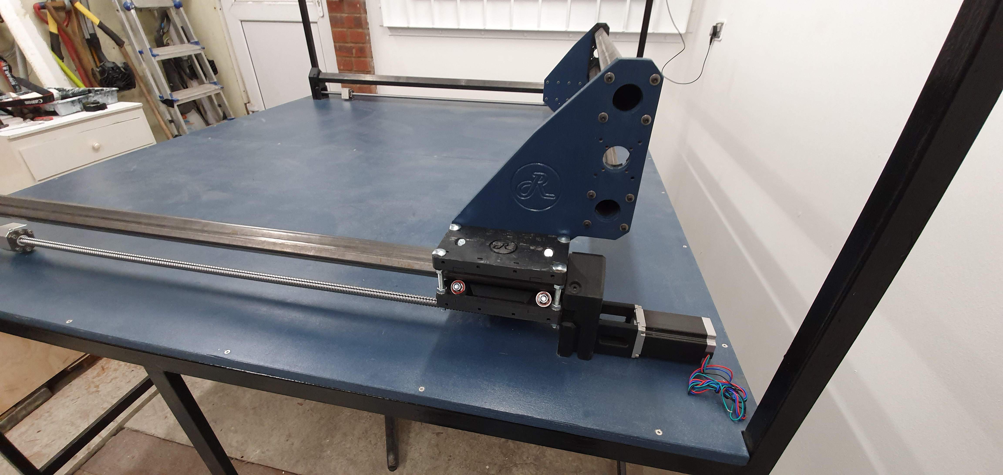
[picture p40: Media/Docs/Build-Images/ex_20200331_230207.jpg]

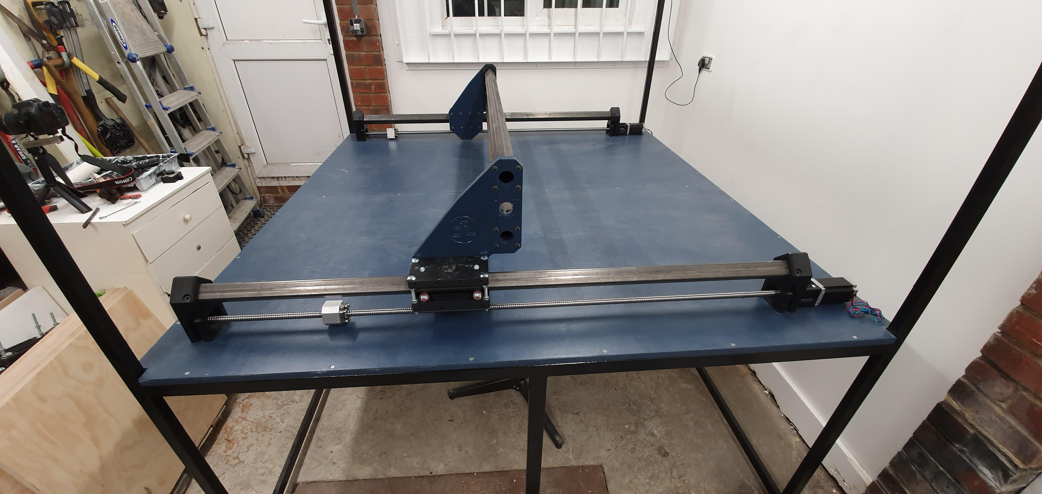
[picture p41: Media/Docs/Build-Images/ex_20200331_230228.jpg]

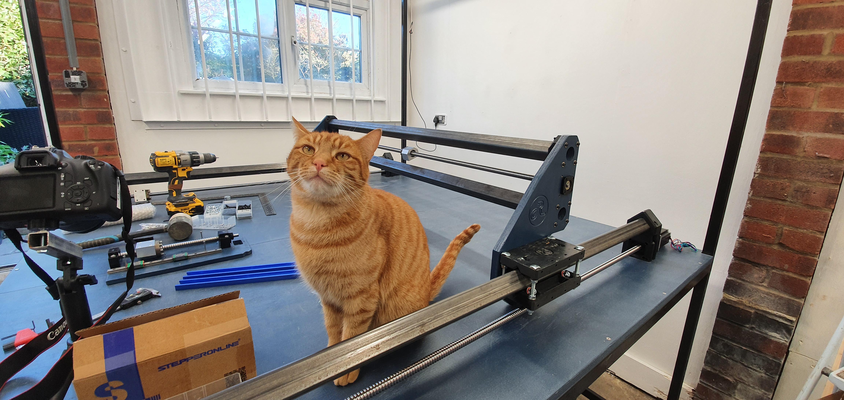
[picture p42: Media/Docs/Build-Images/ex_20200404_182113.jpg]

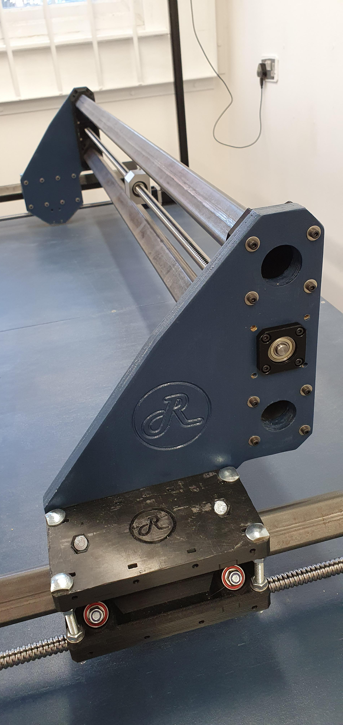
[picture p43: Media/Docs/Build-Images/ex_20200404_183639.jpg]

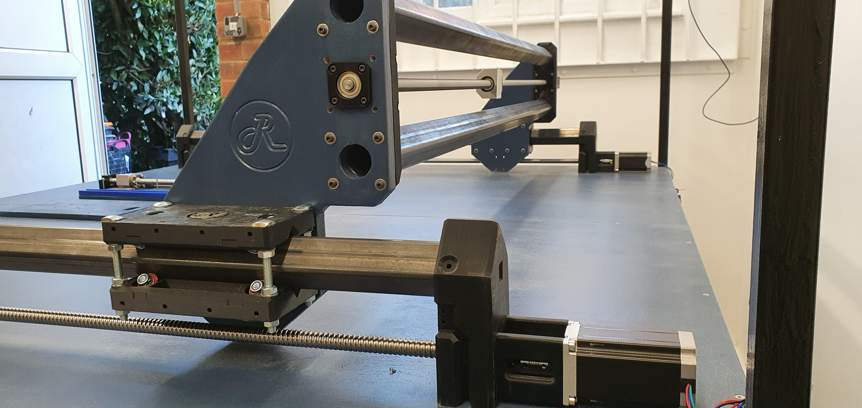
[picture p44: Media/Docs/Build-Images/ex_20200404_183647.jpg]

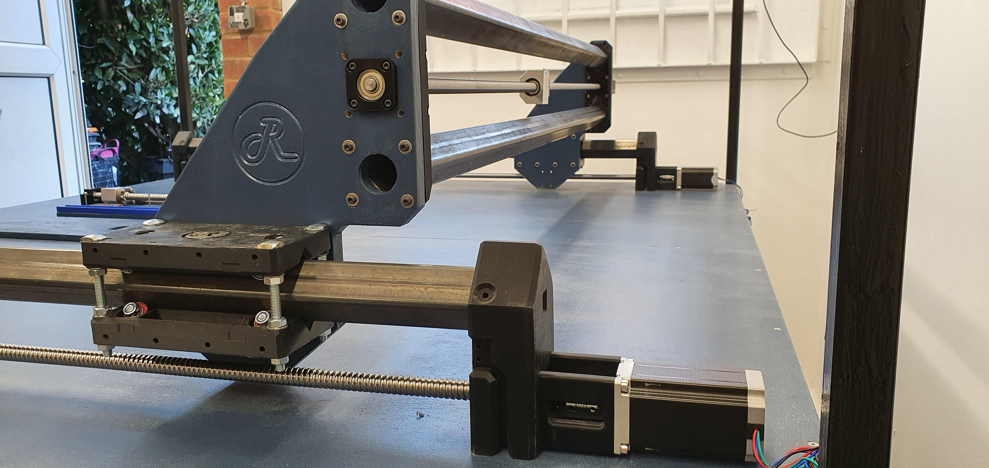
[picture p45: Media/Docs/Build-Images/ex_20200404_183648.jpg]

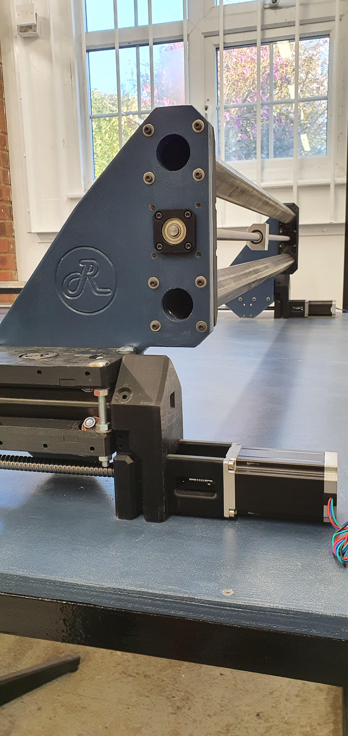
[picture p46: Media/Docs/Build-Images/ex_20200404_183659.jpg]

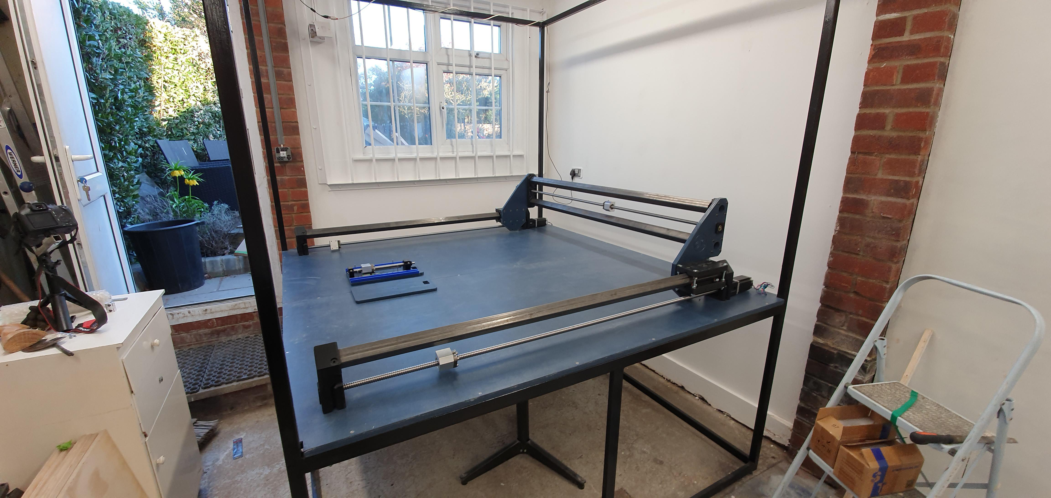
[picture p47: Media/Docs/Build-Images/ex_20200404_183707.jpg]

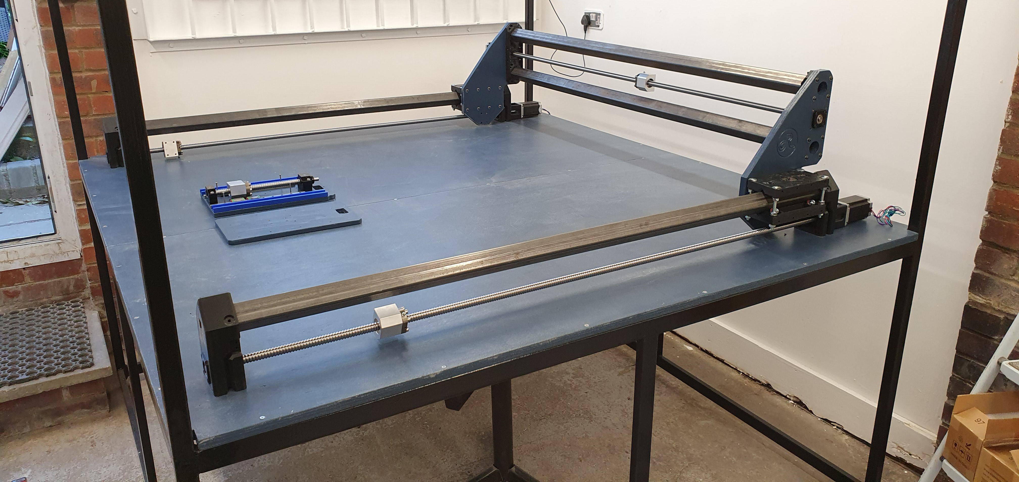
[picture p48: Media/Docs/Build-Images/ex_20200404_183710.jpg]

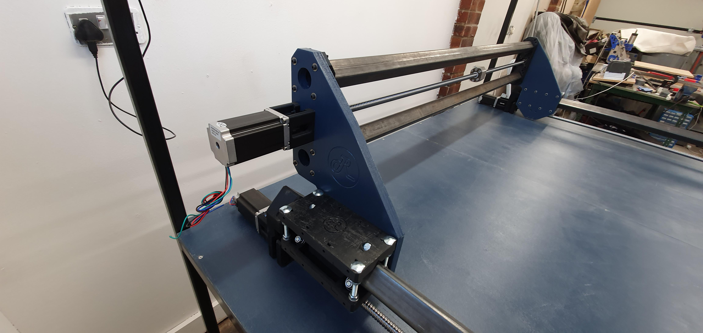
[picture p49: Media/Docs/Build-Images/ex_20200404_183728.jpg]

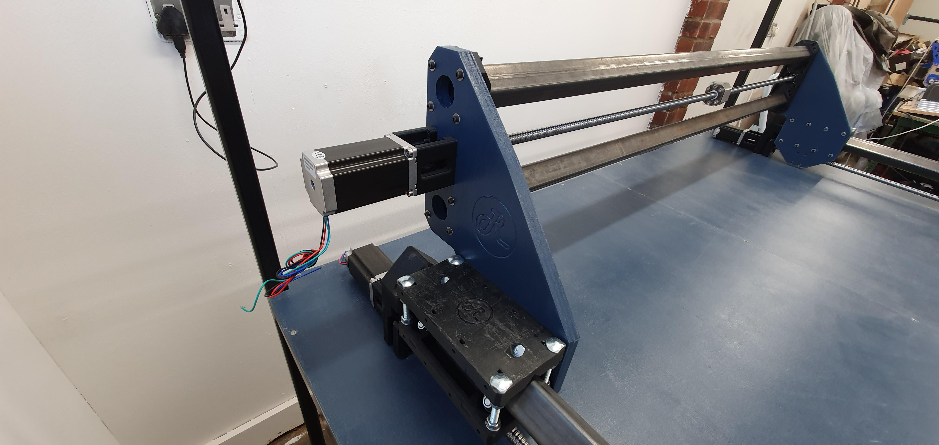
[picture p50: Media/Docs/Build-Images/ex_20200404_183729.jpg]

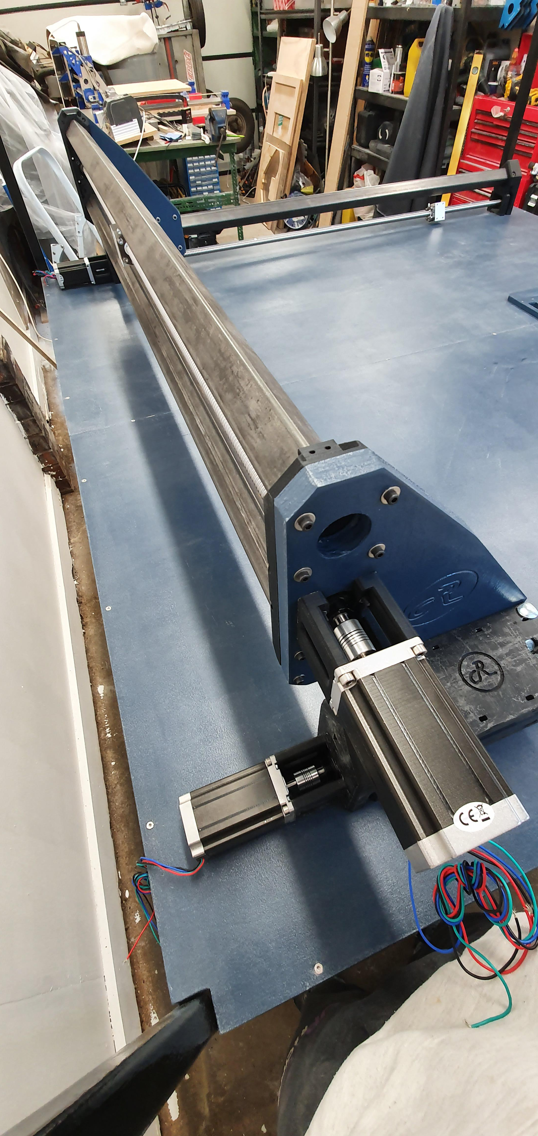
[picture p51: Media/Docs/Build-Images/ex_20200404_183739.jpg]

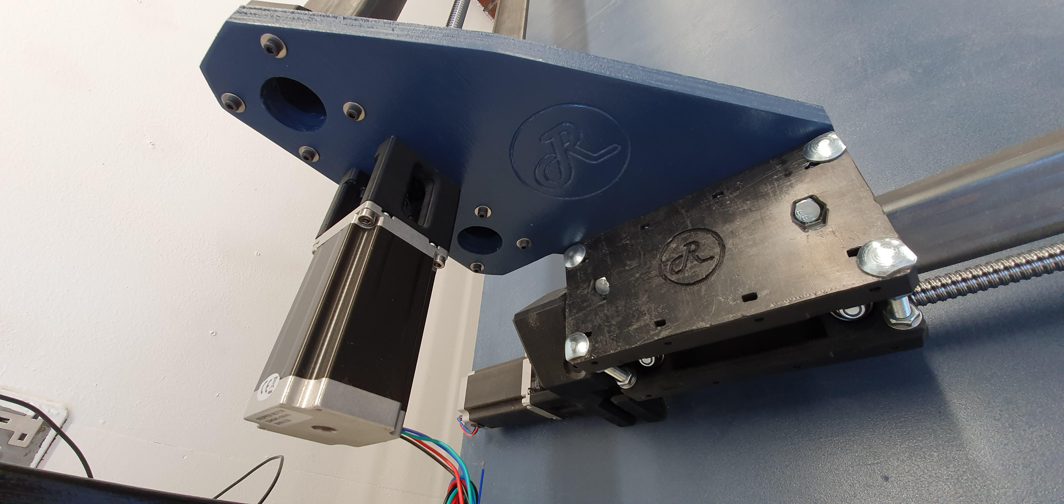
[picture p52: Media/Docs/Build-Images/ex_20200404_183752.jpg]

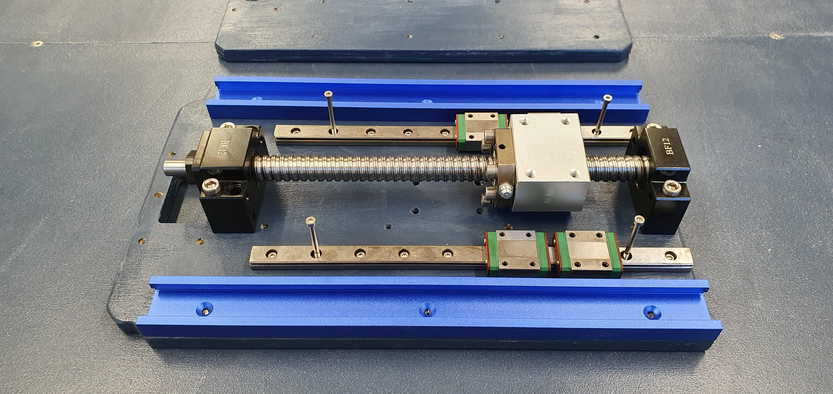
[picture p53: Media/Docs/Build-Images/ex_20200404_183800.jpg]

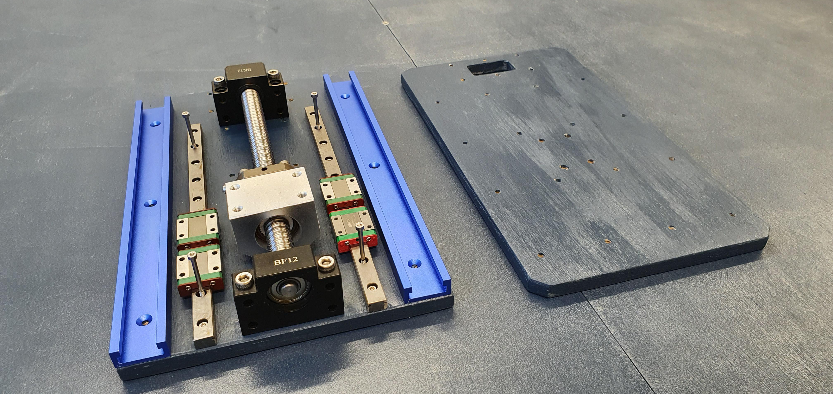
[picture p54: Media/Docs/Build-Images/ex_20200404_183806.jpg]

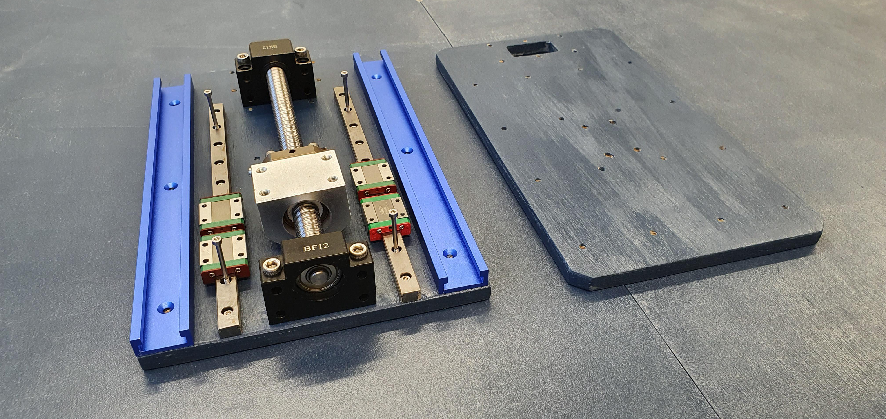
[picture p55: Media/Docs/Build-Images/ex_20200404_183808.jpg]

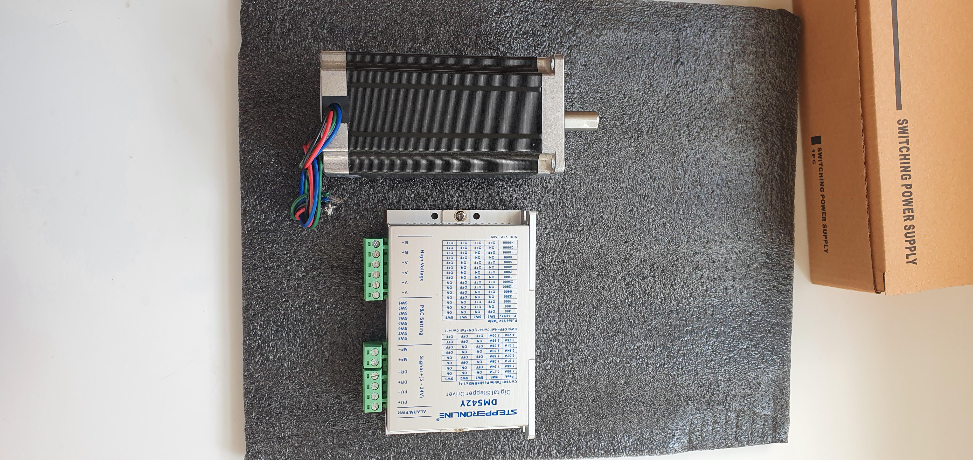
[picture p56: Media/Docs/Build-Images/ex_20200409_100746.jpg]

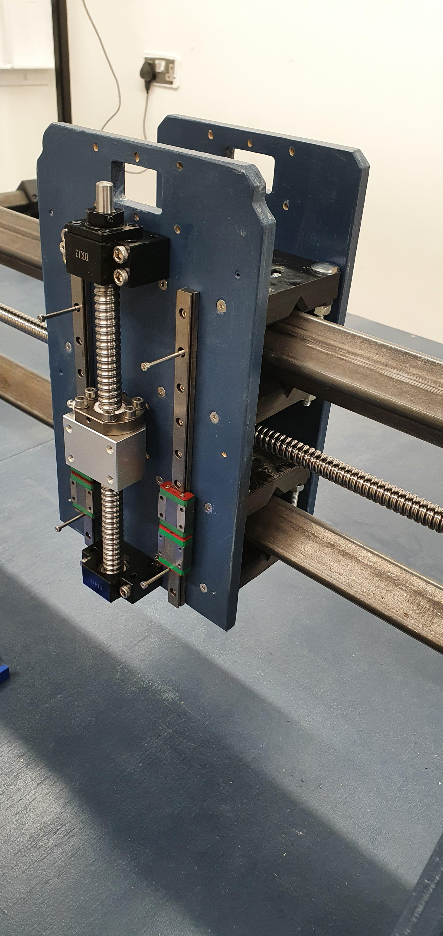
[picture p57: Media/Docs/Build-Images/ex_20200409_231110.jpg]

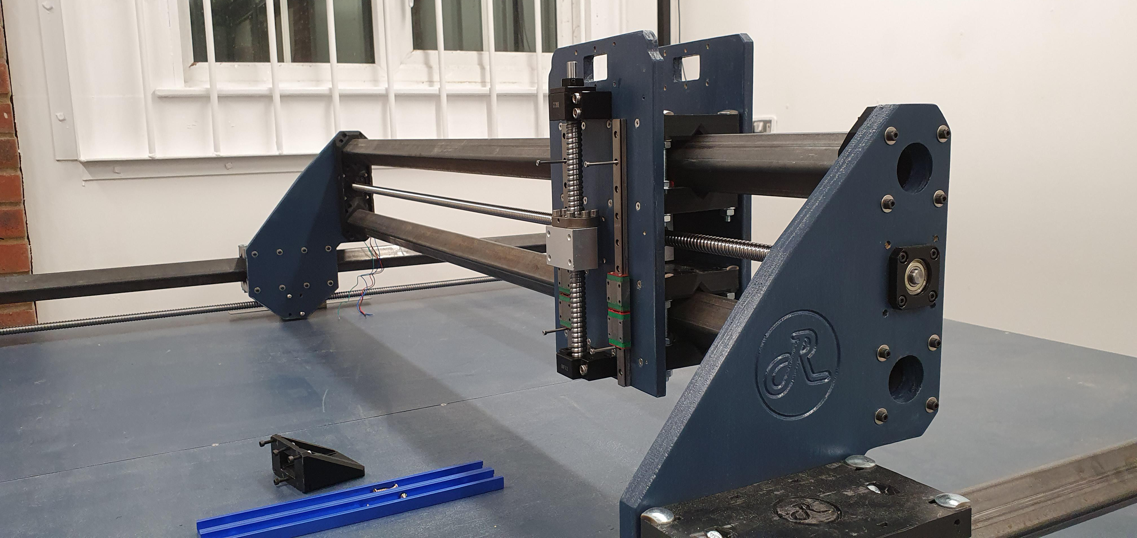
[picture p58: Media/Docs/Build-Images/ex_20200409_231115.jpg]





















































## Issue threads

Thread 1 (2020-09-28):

80mm Spindle

marianoronchi, 2020-09-28:
Pete I'm planning to make an R4 and my spindle has an 80mm diameter. Do you believe that it's possible to get the 80mm version of the spindle mount if not, no problem I will redraw it. By the way I'm creating a complete 3D model of it so if you want it just let me know the file format that you prefer.

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

Thanks!

RootCNC, 2020-10-12:
@marianoronchi Hi, the 3D model is looking niceeee!

I have since added a new commit to the project for an 80mm Spindle - [LINK](Source/STL_Files/Z_Axis_MotorMount_85mm.STL)

I've not printed this nor do I have a 80mm spindle; please could you let me know how this goes?

I'll leave this issue open until I hear its alright.

RootCNC, 2020-10-13:
Incorrect file name was updated - please see this [LINK](https://github.com/RootCNC/Root-4-CNC/blob/master/Source/STL_Files/Spindle_Mount_80mm.STL)

RootCNC, 2020-12-18:
has anyone printed this file - was it ok?

marianoronchi, 2020-12-19:
Pete I'll print it this week, let you know... Best regards.

marianoronchi, 2020-12-28:
> has anyone printed this file - was it ok?

Pete, I just printed the 80mm spindle mount (Some pictures attached) everything looks ok, I just printed it without supports so on the vents the piece has some glitches. Mi spindle it's really heavy and regardless that I'm used ABS, 4 perimeters, 50% Infill, and 4 top/bottom layers I have the sensation that the piece is not strong enough, but I'll give it a try and let you know.

Best regards and thanks for your hard work.

Have a happy new year.

RootCNC, 2021-01-03:
@marianoronchi - Those settings seem about right, well at least what I was expecting anyway. The print looks useable from the photos with the absence of support materials! nice work. it'll be interesting to know the feedback of mounting it into the carriage blocks - mine was a little fiddly and I think this carriage might be a tad harder.

Happy new year too :)

readeral, 2021-06-25:
@marianoronchi did the spindle mount work out for you?

Woszu1981, 2022-01-20:
marianoronchi can you share a complete 3D model?

Closed 2021-02-15.

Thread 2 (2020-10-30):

38mm steel tube for US market

colemanomartin, 2020-10-30:
In the US market 38mm square steel tube is standard. Is it possible to reduce the dimensions of the steel tube mounting points from 40x40mm to 38x38mm (by only moving each wall in by 1 mm) without altering the other mounting points for the carriages and ball screws? If so, a second set of STL files sized for mounting the Y and X rails would expand the reach of this project without significantly reworking the design.

colemanomartin, 2020-11-01:
As I'm looking at this, decreasing to 38mm square tube will reduce the distance between the two halves of the carriage. By my calculation the distance decreases by 2.83mm.  This changes the placement of half of the carriage mounting holes on the side panels and the  Z axis wood panels.  In theory, the upper or lower line of those carriage mounting holes could be changed to slots to accommodate for the two different widths of the carriages. Not sure how people would feel about that. It could make things a tiny bit less stiff.

RootCNC, 2020-11-15:
I think my preference would be to keep the side and front/ rear panels the same between the two configuration and have the 3D printed parts change in size. This should be easy to configure in the software.

RootCNC, 2020-11-15:
The updates files can be tracked here - https://github.com/RootCNC/Root-4-CNC/tree/38mm-Dev

RootCNC, 2020-11-15:
Here are the files I expect to be impacted by the change:

- [ ] X_Axis_Mount_FF
- [ ] X_Axis_Mount_FK
- [x] Y_Axis_Mount_FF12
- [x] Y_Axis_Mount_FK12
- [ ] XY_Carriage_Coach
- [ ] XY_Carriage

Please note - I have no plans of testing these parts, I will require some sort of feedback from the community :)

The files will be in the 38mm-Dev branch of the project until I have feedback on the parts.

colemanomartin, 2020-11-18:
Thank you.  I have a friend also starting a root 4. I'm sharing this with him. One of both of us should be able to test.
________________________________
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

THUNDER351, 2020-11-25:
I only see 2 of the 6 part that you expected to change.

RootCNC, 2020-12-06:
Please see the update - please can you give me feedback on these parts? once I know they work i'll move the out of the DEV folder

RootCNC, 2020-12-06:
Link to the files are [HERE](https://github.com/RootCNC/Root-4-CNC/tree/38mm-Dev/Source/STL_Files/38.1x38.1mm%20Box%20Section%20(1.5x1.5%20inch))

THUNDER351, 2020-12-06:
I will get them printed soon. Been printing the other parts. I will let you know how they work. The first two parts you made the changes to worked on the 1-1/2" x 1-1/2" tube I plan to use.

BayouBurner, 2021-01-22:
Printed the y-axis mounts and they are too tight to use. My stock is exactly 1.5"m(38.1mm) but the part is a bit under. Could be shrinkage? Printed metric versions and they fit fine, I may add a tape sleeve to perfect the fit but its fine as is.

colemanomartin, 2021-01-22:
With what material did you print?

BayouBurner, 2021-01-24:
Black PETG.  I may be heading in the wrong direction, but I'm printing and using the std 40mm parts with 38.1 tube and its all fitting together fine. My biggest worry was the carriage sets fitting on the side plates and still being adjustable but it was perfect.
Same for Z panels, fit is great. There is some play in the y axis mounts, but I plan to use the hold down bolts to make the fine adjustments. Time will tell.

RootCNC, 2021-01-24:
It might seem your printer isnt printing to scale perfectly?

BayouBurner, 2021-01-24:
Everything is lining up perfectly. The tubes are galvanized. They don't mic oversized (on my cheap mic) but that might explain things.
Sent from my iPhone

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

BayouBurner, 2021-01-25:
Actually I did use the 38.1 versions of the carriage. Sorry for the confusion. I ground off all the galvanize on a scrap piece and it was still too tight.

markamace1, 2021-05-12:
I am using 1.5 inch square aluminum tubing.  Printed off X_Axis_Mount_FK_38.1mm and it's quite tight, but fits.  I used a file to clean up the edges of the tubing and wiggled the printed off piece on most of the way by hand.  I believe a small rubber mallet will do nicely for the final bit (See pic below).

I will print the Y_Axis_Mount_FF12_38mm this weekend.  My printer claims it will take 24hrs to print and the 3D printer is in my home office.  I prefer not to have it running during work hours when I might have meetings.

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

RootCNC, 2021-05-15:
I rubber mallet is expected from my experiences - it ensures it has a nice tight fit.

I must admit - I don't like leaving my printer on un attended, just because I don't trust it too well.

maybe I need to revisit the sizing for these parts and double check - how much material did you remove??

markamace1, 2021-05-16:
The aluminum square tubing was just a bit rough from cutting.  I ran a flat file along the edges and corners a couple times just to deburr.  It's a nice snug fit, snug enough you have to have it lined up square to get it to slide in.

I am not sure I would change the measurement any.  I've had other things come up, so I won't be able to print the other parts as planned until next weekend, maybe longer.  I will come back and update when I have them printed.

ProudPoppaG, 2022-10-22:
Could you tell me the wall thickness of the 38.1" you are using?

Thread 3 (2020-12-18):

Recommended / Tested Infill %?

Xgl0baltk, 2020-12-18:
Could the recommended Infill (if there are any preferences stress and durabilitywise) be added to the BOM?

Just slicing right now,
1x Y_Axis_FF 1x Y_Axis_FK
0.6 nozzle, 0.32mm Layer hight 50mm/s
50% Gyroid infill: 1 day 11 hours  659gr
40% Gyroid infill: 1 day 6 hours 6 Minutes 531gr
30% Gyroid infill: 21 hours 58 minutes  453gr

quite a difference at just 2 parts and yes i am biased towards Gyroid since it is pretty :) and can take a lot because of the changing infill direction

RootCNC, 2020-12-18:
The Root 4 is based heavily on the Root 3 CNC machine - please check this out for my recommendation - [Link](https://rootcnc.com/machines/root-3/how-to-print-r3/)

Closed 2020-12-18.

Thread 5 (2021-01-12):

69mm Router Mount Needed

BayouBurner, 2021-01-12:
Need a 69MM router mount for my Root 4 to mount a Makita RT0700, but only see that for the root3 on Thingiverse? Any guidance would be much appreciated.

RootCNC, 2021-01-12:
Hey, please see the latest commit to this repo - [HERE](https://github.com/RootCNC/Root-4-CNC/commit/56f9f0ad2770f859b4f236fa709d6582033cf9ab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)

let me know if you have any issues with the part - I'll leave this issue open until I hear some feedback to ensure its a good part.

BayouBurner, 2021-01-13:
Thanks !
It may be a few weeks before I can provide any feedback on the part, but just getting the STL is a HUGE help.

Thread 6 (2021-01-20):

Need a foot plate for the Y-Axis mounts.

BayouBurner, 2021-01-20:
My table for the Root 4 is made from thick lumber framing and I don't have access to the underside of the table where the Y-axis mounts go. I need to be able to fasten them down from the top. Would it be possible to get an STL file of a plate I can attached to the existing mounts from below using the existing holes and hardware, that have a extension to the inside where I can access them from above?  I could probably make them from wood, but prefer to use the same material as the rest of the unit.  Thanks in advance for the support!

Closed 2021-01-24.

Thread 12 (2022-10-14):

Modification suggestion for Carriage

masterxq, 2022-10-14:
I have a modification suggestion for the carriages:
My model look like this:
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

The main modification is that the Force will not be transferred into a small area of the Plastic as it will be in the current version.
With the modifications the Force will be evenly distributed and caught by the M8 bold and the side panels.
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

The underlying m8 bold would go from one side to the other.

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

In a prototype I used severed m8 threaded rod. This is very cheap and there is no need for a Nut if the holes have a diameter of 7.6 mm - 7.7 mm. This will hold itself.

The to bold in the middle don't need to be M8.

Advantages:
- Much stiffer
- Much more stability
- Much fewer requirements on the printed part
- Likely much better durability
- No need for the nuts
- If m8 threaded rod will be used it is cheap
- Faster Printing

Disadvantages:
- Needs modifications on the side panels
- Much stiffer, what could cause problems if the square tube is irregular
- Maybe slightly harder to build

It is possibly to use normal infill and wall thickness and have higher wall thickness and infill directly on the ball bearing.

Additionally, it could be helpfully to add a hole under the button ball bearings to be able to easily remove dirt and easily grease the bearings. The holes can also be added to the top carriage, but they should be covered on normal operation.

I did my best to find the correct word to write this, I would like to apologize for any mistakes in the wording :)

Regards

masterxq, 2022-10-14:
Here is my zipped FreeCAD model:
[Carriage.zip](https://github.com/RootCNC/Root-4-CNC/files/9789703/Carriage.zip)

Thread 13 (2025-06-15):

BOM links are broken

Subn3tmask, 2025-06-15:
I am a US user wanting to take my current CNC and re-create the structure.. and i was wanting to look at the links, and most of them in the BOM are broken.

Thanks

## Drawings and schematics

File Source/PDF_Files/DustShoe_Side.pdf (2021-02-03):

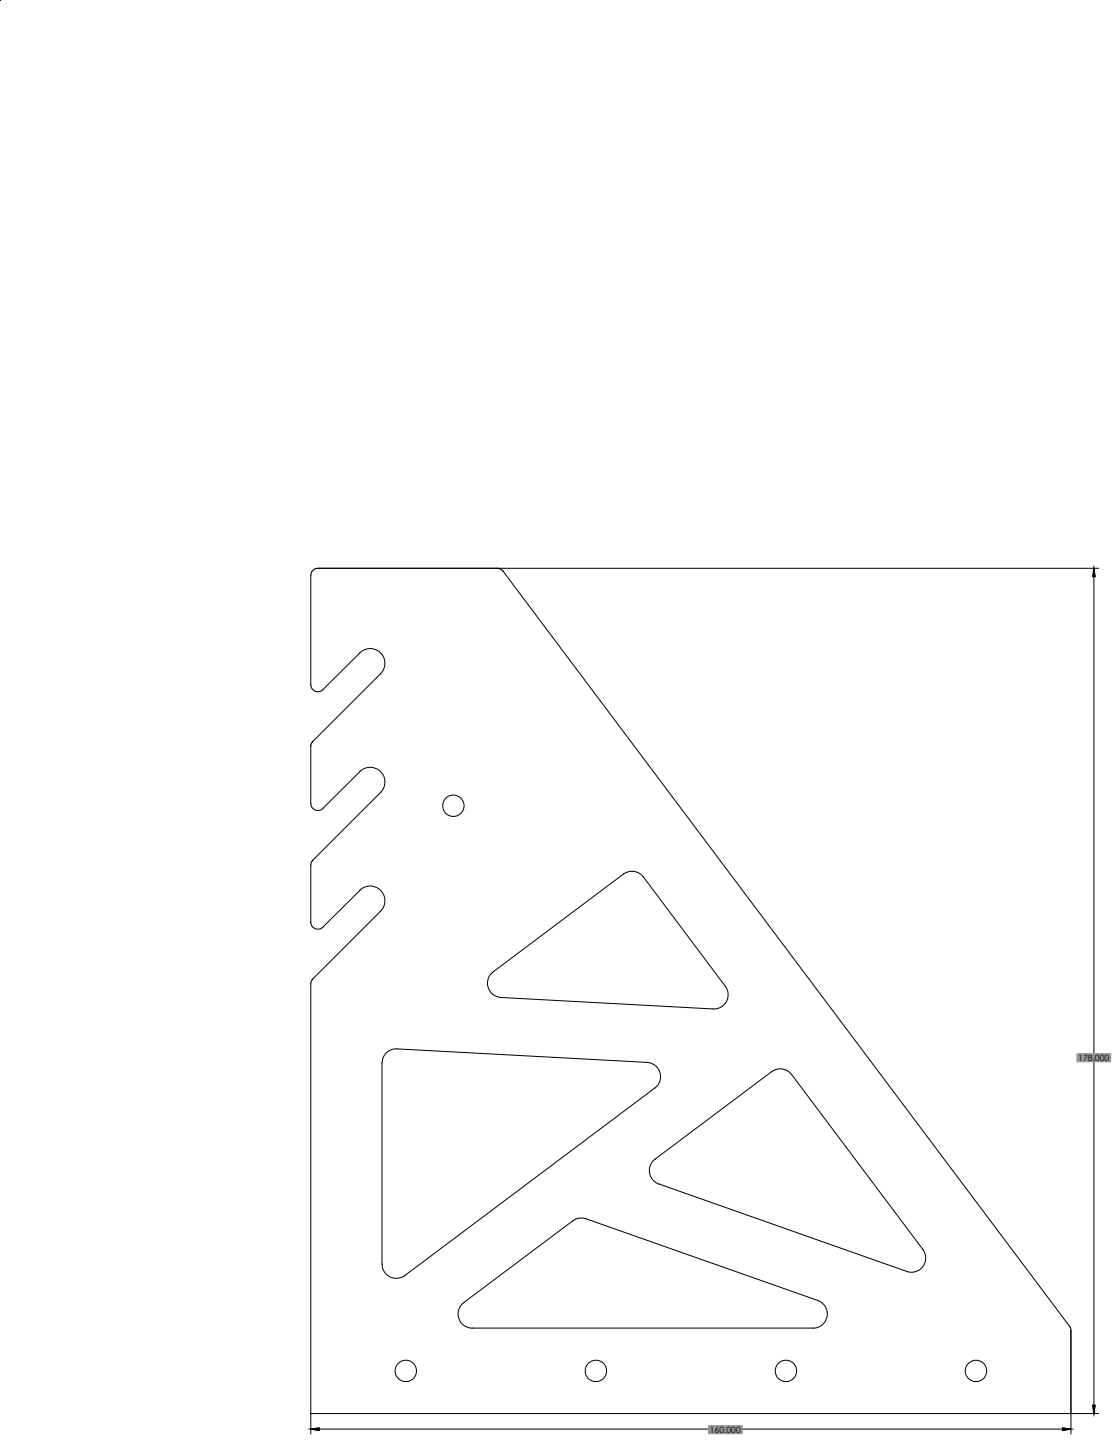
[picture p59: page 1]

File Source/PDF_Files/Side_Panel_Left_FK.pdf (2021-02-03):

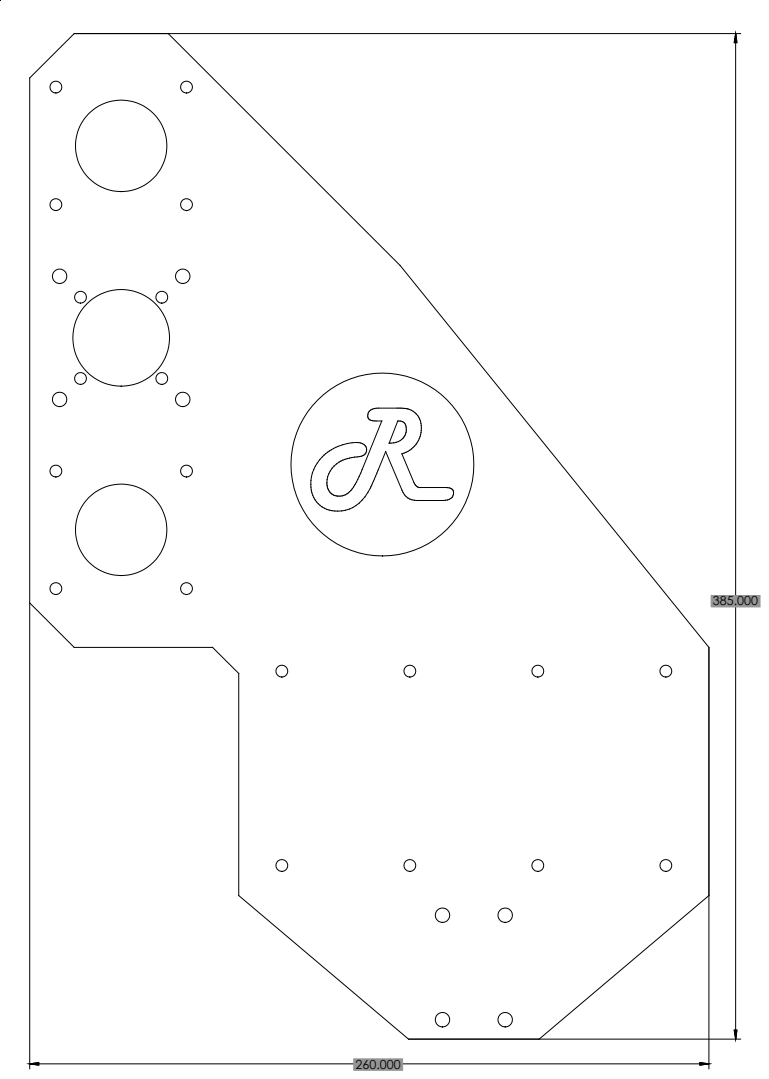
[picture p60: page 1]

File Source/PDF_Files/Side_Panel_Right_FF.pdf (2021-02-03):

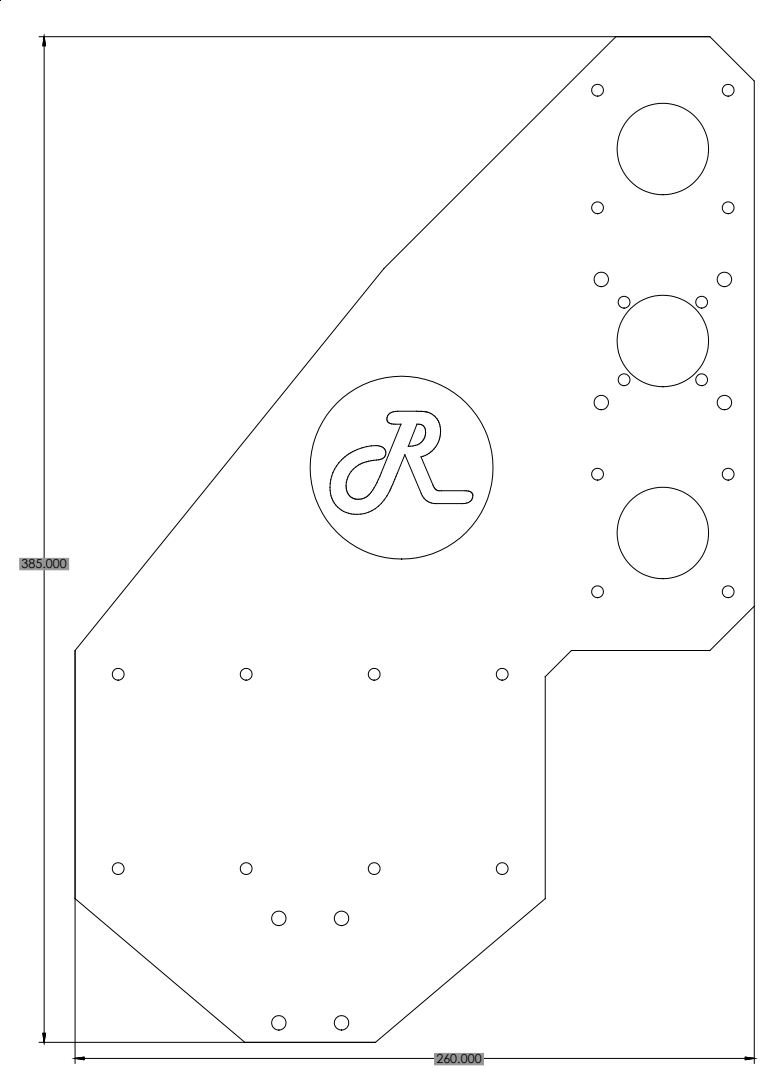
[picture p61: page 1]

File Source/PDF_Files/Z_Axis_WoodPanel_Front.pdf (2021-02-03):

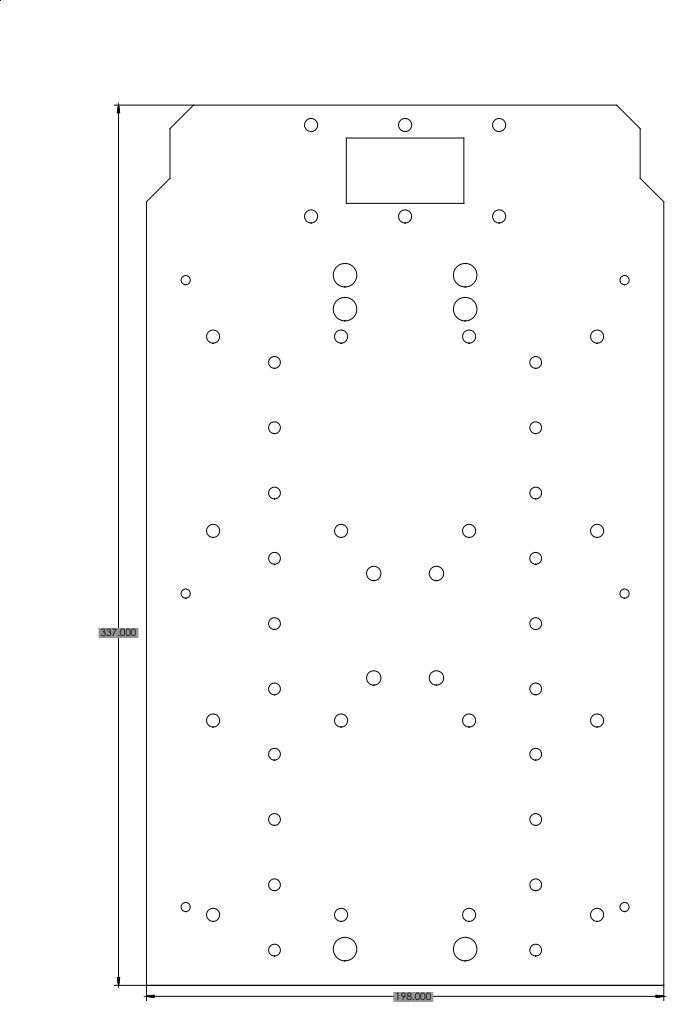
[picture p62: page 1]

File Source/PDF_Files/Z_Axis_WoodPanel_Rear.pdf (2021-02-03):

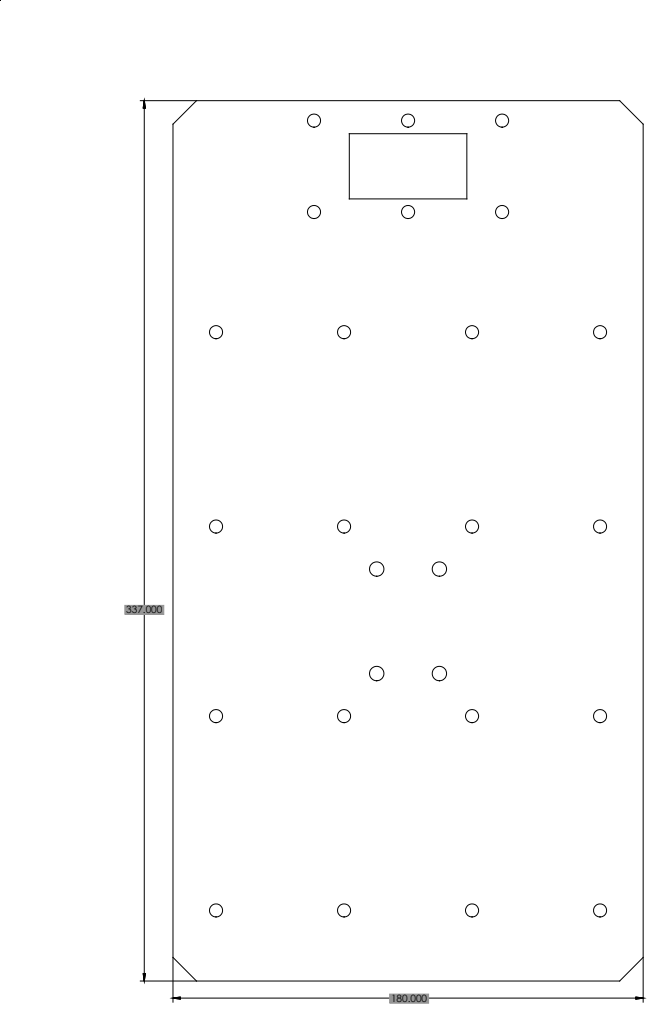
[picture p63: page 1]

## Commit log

2020-06-30 Issue 1 release
    [DustShoe_Side.DXF, DustShoe_Side.STL, DustShoe_T_SlotTrack.STL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]
2020-07-01 Added BOM details #1
2020-09-09 Update README.md
    Minor update to the BOM
2020-10-13 Name change
    [Spindle_Mount_80mm.STL]
2020-10-17 Create Working Area.xlsx
    Added a spreadsheet to help users’ workout the length of the: Box Section VS Working Area VS Ballscrew Length
    [Working Area.xlsx]
2021-01-12 Create Spindle_Mount_69mm.STL
    Added Spindle mount to accommodate a 69mm Spindle
    [Spindle_Mount_69mm.STL]
2021-02-14 Added Dust Show Base to the Repo
    [DustShoe_Base.DXF]
2021-07-27 Update BOM
    [XY_Axis_BallScrewMount+0.25.STL, XY_Axis_BallScrewMount.STL]
2021-08-13 Adding 55mm M5s
2023-02-21 Added BOM
